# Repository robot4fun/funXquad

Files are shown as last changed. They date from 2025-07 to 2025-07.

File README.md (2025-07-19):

<p align="center">
  <picture>
    <source media="(prefers-color-scheme: dark)" srcset="funxedu-logo4-white.png">
    <source media="(prefers-color-scheme: light)" srcset="funxedu-logo4-black.png">
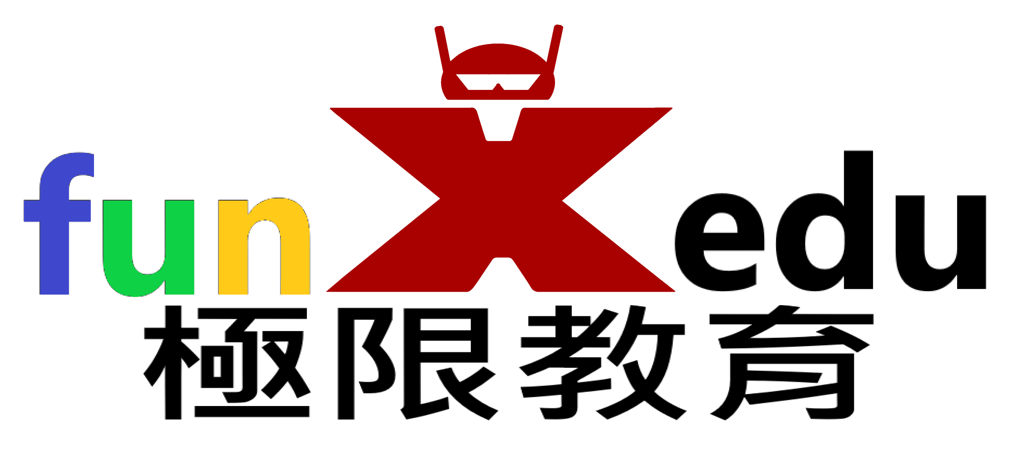
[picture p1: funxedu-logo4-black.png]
funXedu
    
  </picture>
  <br/>
</p>

funXquad 是一個低成本、DIY（自己動手做）的無人機項目，專為教育用途設計。

!! 此專案授權僅限個人或學校教學非商業用途。嚴禁任何商業使用、分發或用於商業目的之修改 !!

## 專案目錄結構

以下是 funXquad 專案的主要目錄及其功能：

* `frames/`: 無人機機架的3D列印檔案。

* `v1/`: 專案的第一個版本。
    * `firmware/`: 存放無人機的韌體檔案。
    * `hardware/`: 包含硬體設計檔案，例如電路圖或佈局檔案。

* `funXcon/`: 遙控器程式及相關文件。

* `README.md`: 專案的說明文件。

## DIY 材料清單

有室內和室外兩種類型，除電路板相同外，其餘零件不同。

* `電路板`:
    * `必要`:
        * `洞洞板`: 1個
        * `電池接頭`: 依電池規格 1個
        * `WiFi SOC`:
            * v1: `ESP12S模組` 1個
            * v2: 增加圖傳，努力中..
        * `IMU`: `MPU6050模組` 1個
        * `電晶體`: SI2302 或 NCE3420 4個
        * `二極體`: 1N4148 或 1N5819 4個
        * `電阻`: 1k歐姆以上 4個
        * `電量感測`； 10kΩ以上 1個 + 5倍阻值的電阻 1個
        * `電線`: 少許
    * `選用`:
        * `穩壓模組`:  如果選擇帶有 `3.3V 穩壓晶片` 的 `MPU6050模組` ，可以直接拉出 `3.3V電源` 供電給WiFi SOC。如果沒有，就需要 `1.8V-5V 轉 3.3V 穩壓模組` 1個
        * `室外高度計`: 3.3V BMP280模組 1個
        * `室內高度計`: VL53L0X模組 1個

* `機架`:
    * `室內機`: typeD 需牙籤 1支，切割成10mm長度共 4支
    * `室外機`: 3mmx3mmx500mm 碳纖維空心方管 1支，切割成50mm長度共 4支

* `動力系統`： 需4組
    * `室內機`: 820或8520空心杯馬達直驅 55mm 或 40mm 螺旋槳。螺旋槳孔徑需搭配馬達軸徑，通常是 1mm
    * `室外機`: 馬達採用720空心杯 + 減速齒輪組 + 135mm 螺旋槳。螺旋槳孔徑和形狀需搭配齒輪組軸徑    

* `電池`: 以下為實驗過的建議組合，注意電池和充電器接口需匹配
    * `室內機`: 3.8V 高壓 300mAh 75C 或 380mAh 60C 鋰電池 + 3.8V 充電器
    * `室外機`: 3.7V 600~1100mAh 20C + 3.7V充電器

## 所需工具
* `3D列印機`: 用於製作機架
* `燒錄器`: 用於燒錄韌體
* `焊接工具`: 用於製作電路板
* `熱熔膠槍`: 用於固定馬達，電路板和機架
* `橡皮筋`: 用於固定電池
* `安卓手機`: 用於遙控器安裝

## 製作機架
* 3D 打印零件，檔案在 [`frames`](/frames) 目錄內
* `室內機`:
    * `TypeB`: 共3個打印件
    * `TypeD`: 共3個打印件
    * `TypeE`: 1個打印件

* `室外機`: 共3個打印件
* 初學者建議使用 `PETG` 線材，機架會較有彈性，較耐撞摔

## 燒錄韌體
* `v1`: 
    * 下載韌體檔案 [ `firmware.bin` ](v1/firmware/firmware.bin)
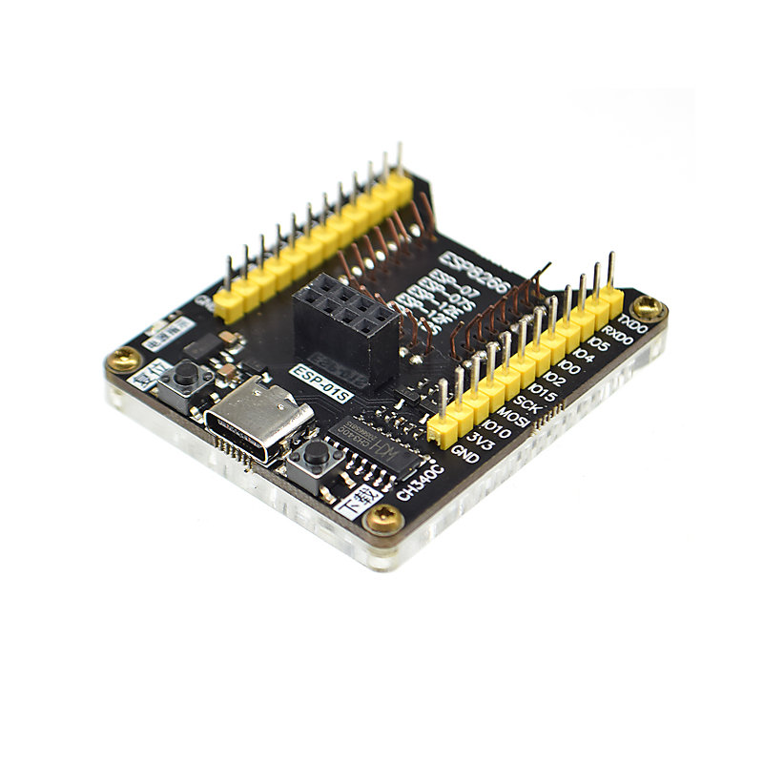
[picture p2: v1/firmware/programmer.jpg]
    * 將`ESP12S模組`正確放入 `燒錄器` 中  (如果使用 `USB to TTL` 或 `開發板` 當燒錄器，請確保接線和電壓正確)

    * 以 `USB 訊號線` (不是充電線) 連接 `電腦` 和 `燒錄器` 
    * 點選進入 [`燒錄工具網頁版`](https://espressif.github.io/esptool-js/)
    * 點選網頁 `Connect` 按鈕，選擇正確的`USB端口` 後點選 `連線`
    * `Flash Address` 設為 `0x0`
    * 點選 `選擇檔案` 按鈕後選擇之前下載的韌體檔 `firmware.bin`
    * 點選網頁 `Program` 按鈕後開始燒錄韌體
    * 燒錄完成後點選網頁 `Disconnect` 按鈕
    * 拔除 `USB` 線後取下 `ESP12S模組`

* `v2`: 增加圖傳，努力中..

## 製作電路板
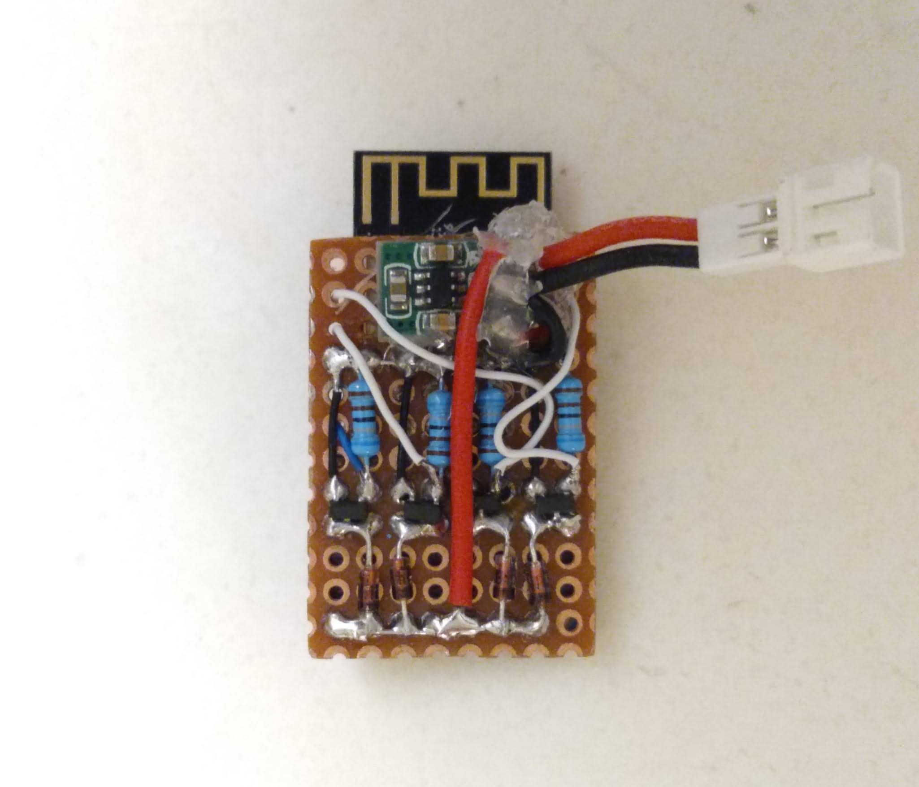
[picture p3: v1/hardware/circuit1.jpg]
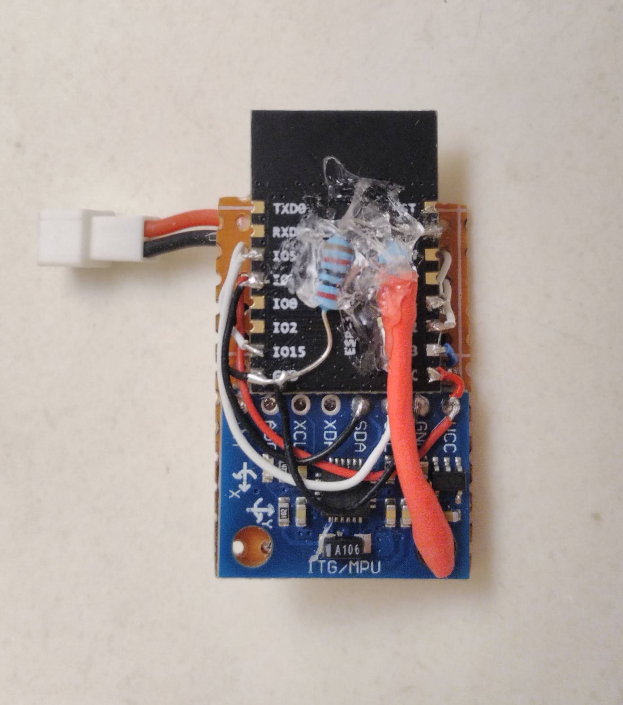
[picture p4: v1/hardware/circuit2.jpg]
* `v1`: 參照 [`原理圖`](v1/hardware/Schematic_funxdrone_v1.pdf) 和成品照自行加工 這張含 `穩壓模組` 

* `v2`: 增加圖傳，努力中..

## 組裝
* `室內機`: 
    
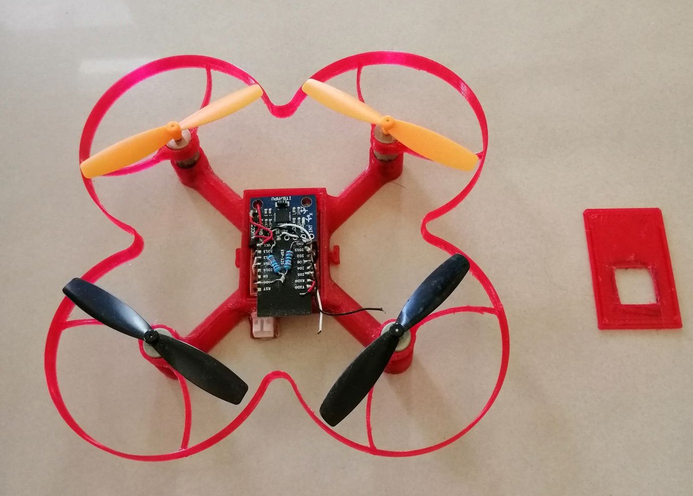
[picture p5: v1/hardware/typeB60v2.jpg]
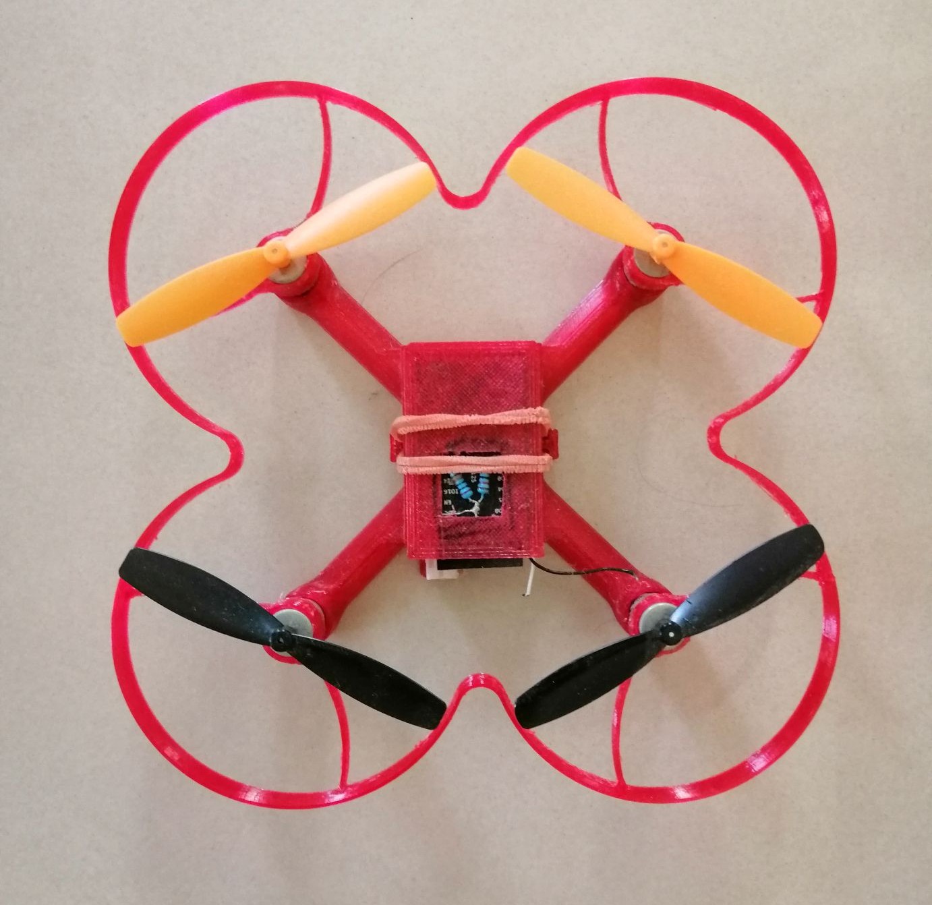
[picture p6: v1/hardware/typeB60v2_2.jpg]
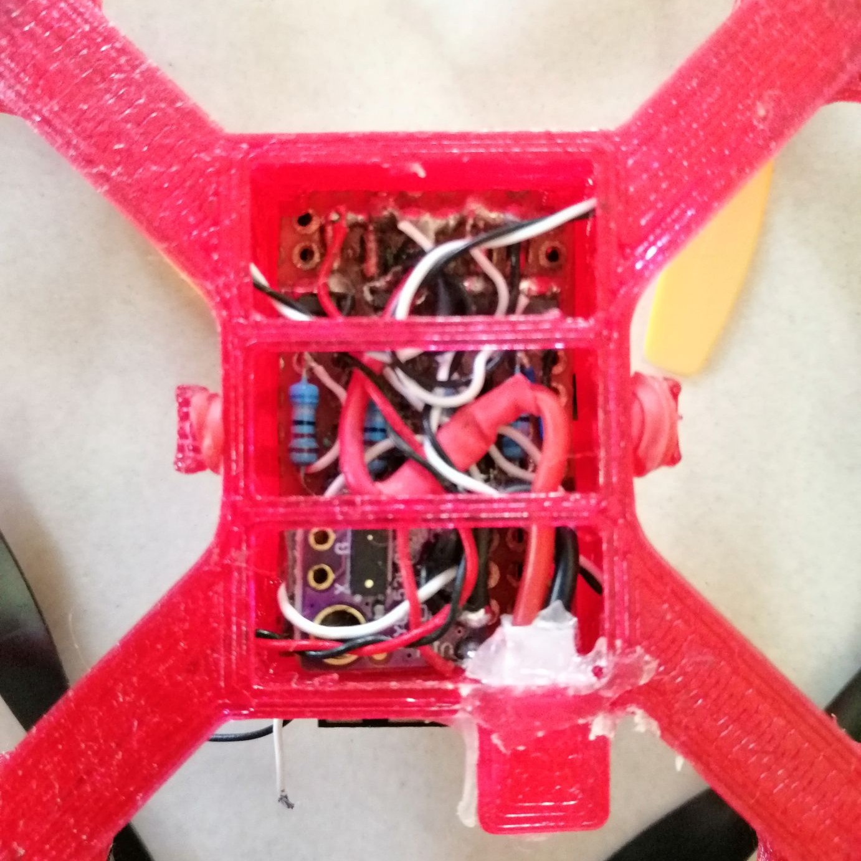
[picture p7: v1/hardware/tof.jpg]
    * `TypeB`: 適用 `55mm` 螺旋槳 這張電路板不含 `穩壓模組` ，由 `MPU6050模組` 自帶的 `3.3V 穩壓晶片` 穩壓 這張照片的螺旋槳是 `60mm`  裝了 `高度計`

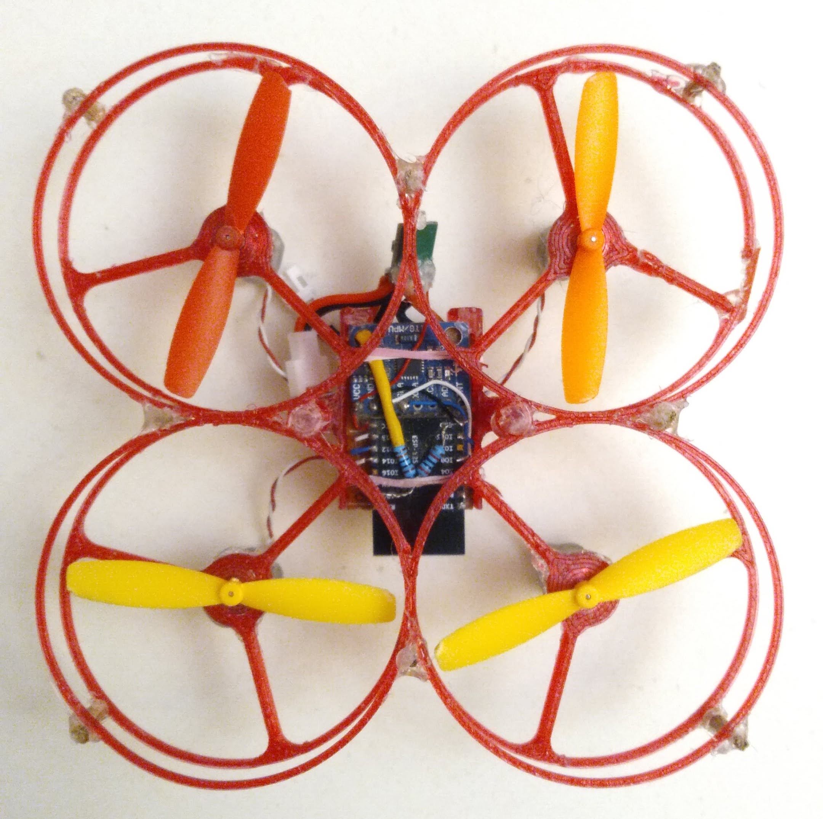
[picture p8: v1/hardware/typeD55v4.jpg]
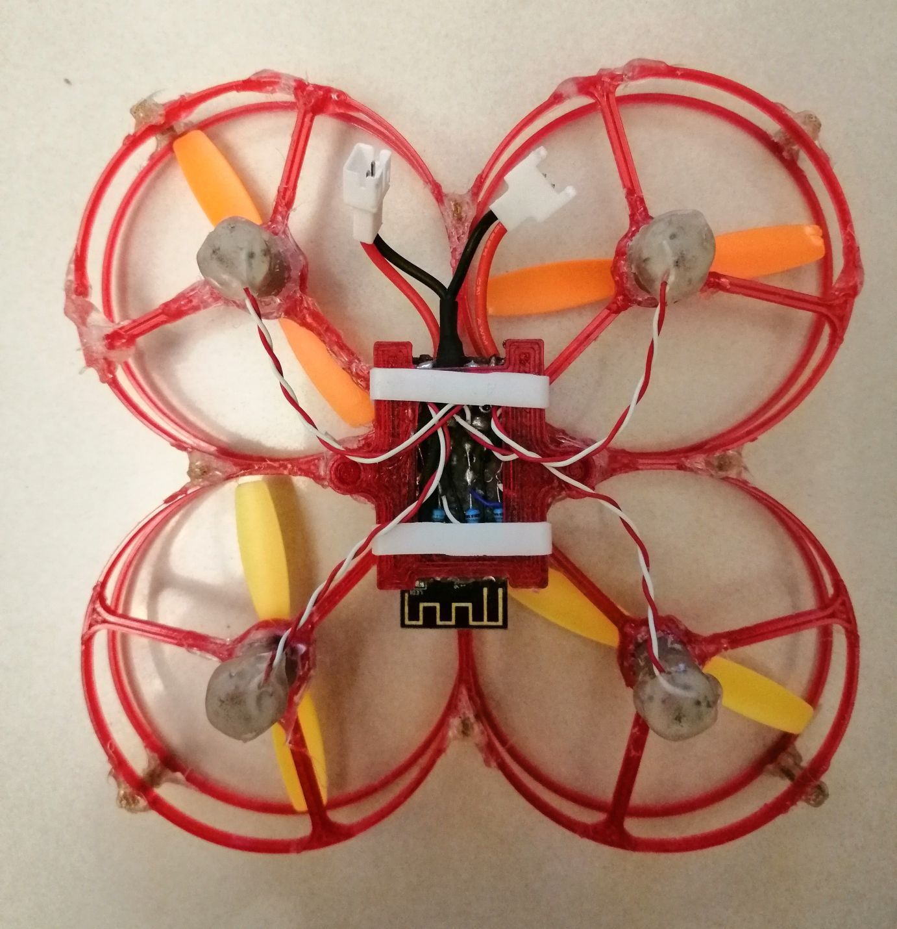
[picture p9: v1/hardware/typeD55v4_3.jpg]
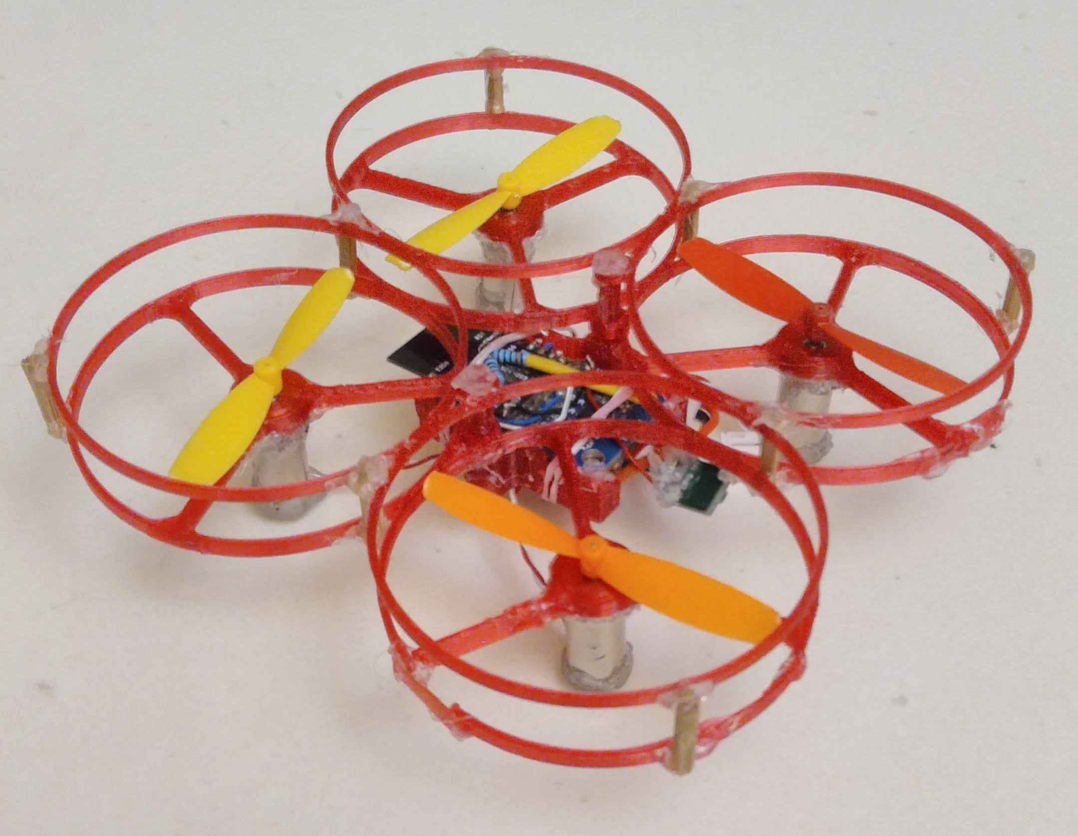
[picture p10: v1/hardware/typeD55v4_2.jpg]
    * `TypeD`: 適用 `55mm` 螺旋槳    
   
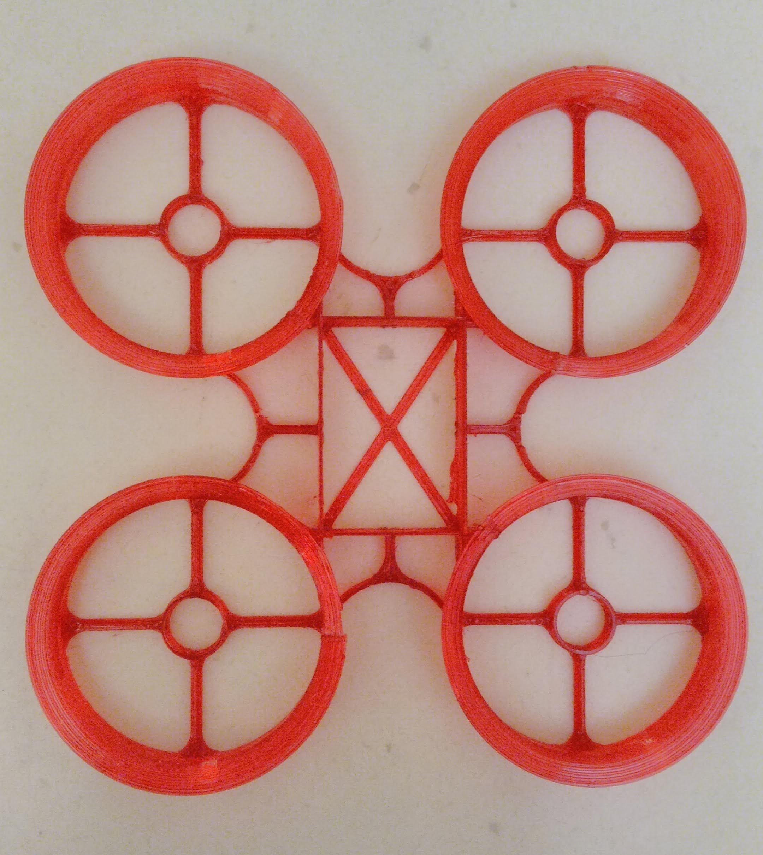
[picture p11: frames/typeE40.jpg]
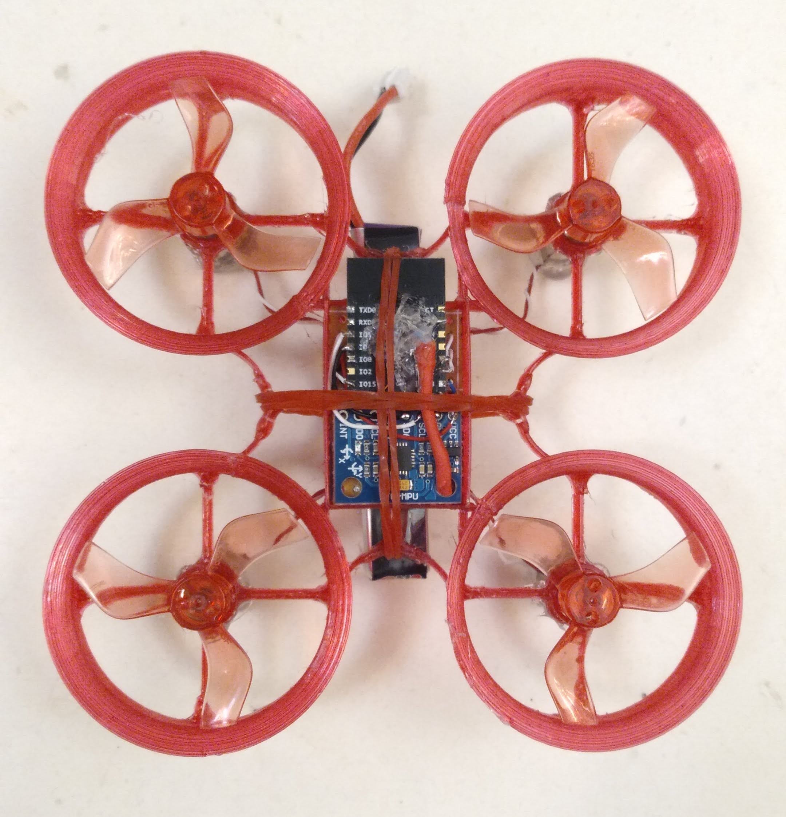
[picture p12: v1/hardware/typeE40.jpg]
    * `TypeE`: 適用 `40mm` 螺旋槳  

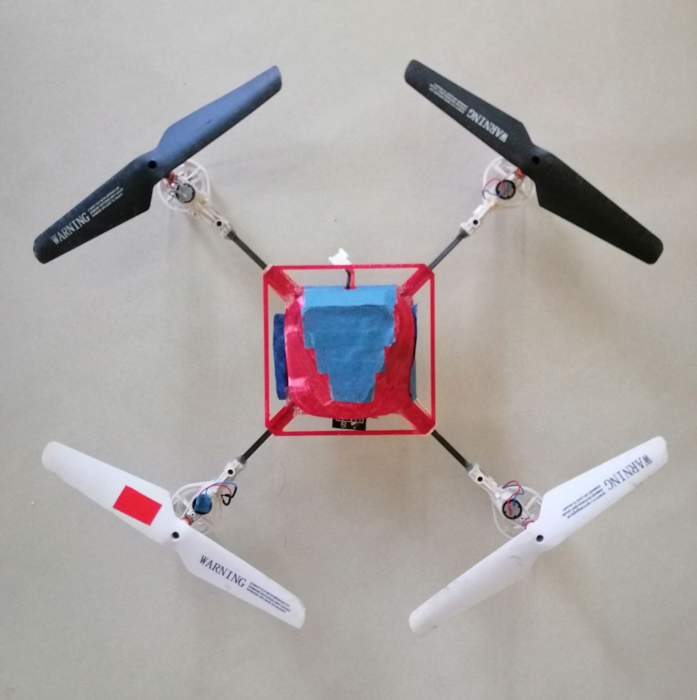
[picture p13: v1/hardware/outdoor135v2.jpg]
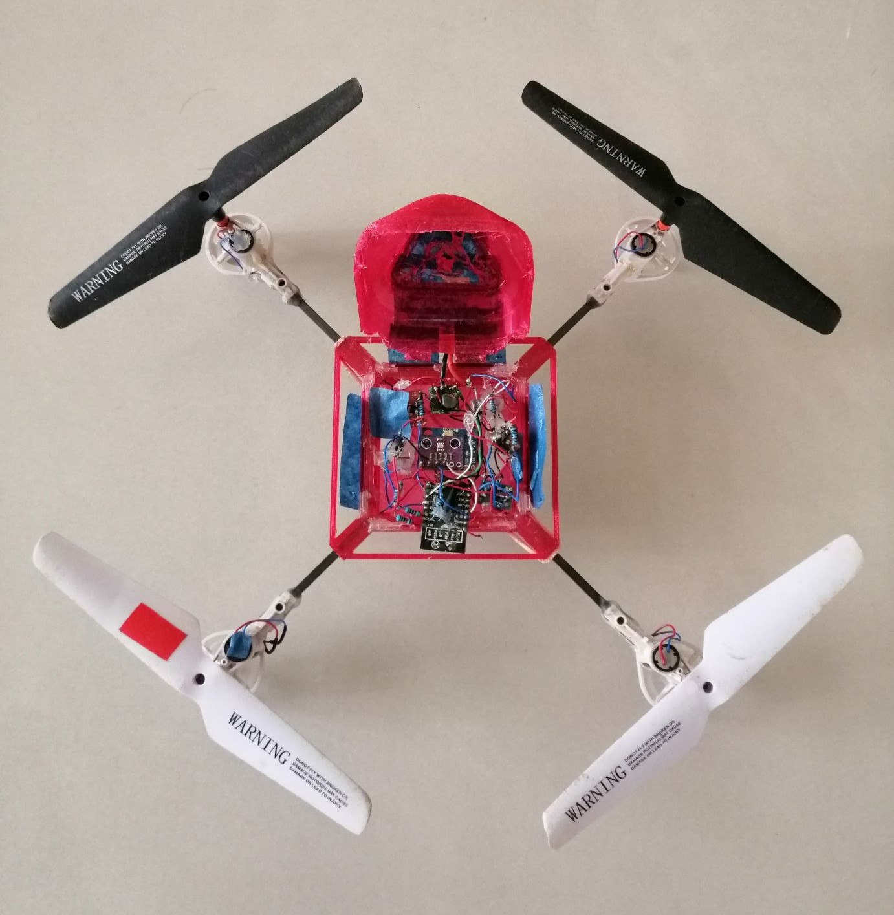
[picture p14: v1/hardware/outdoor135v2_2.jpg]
* `室外機`:   安裝了 `高度計` (線路凌亂，建議還是做好電路板再組裝)

## 遙控器
使用手機當遙控器，目前僅支持安卓10.0以下版本( 從 Android 10 開始，無法透過程式碼啟用或停用 WiFi )

* `安裝`: 先在手機內設定允許安裝不明程式，下載 [`funXcon.apk`](funXcon/funXcon.apk) 後安裝即可

* `使用說明`: 
    * 無人機插上電池 (天線是無人機的尾部)
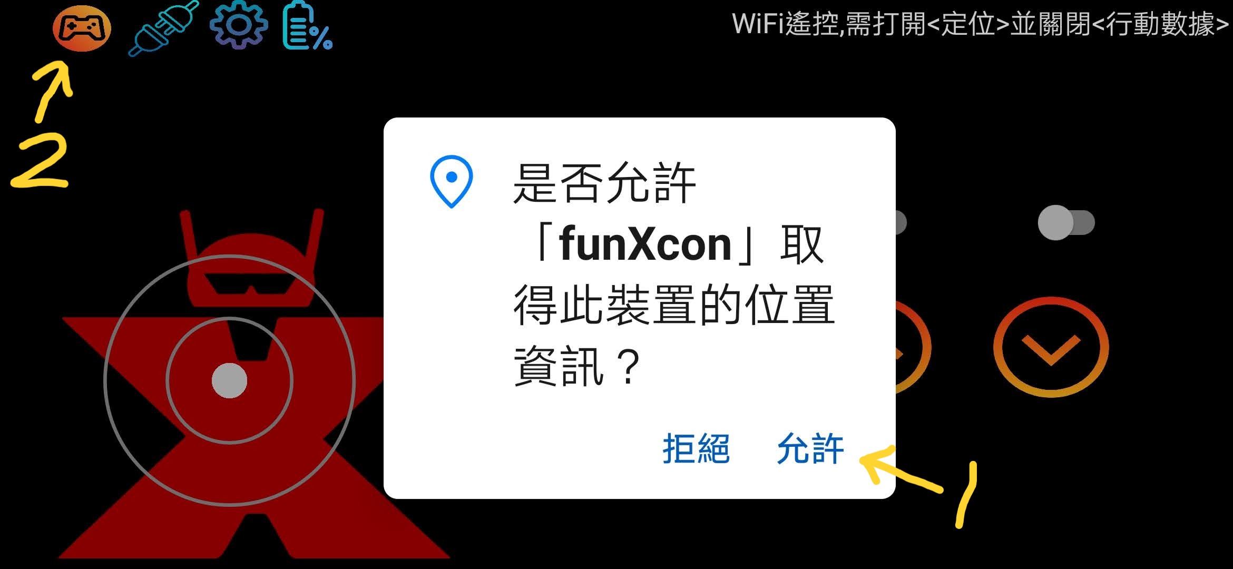
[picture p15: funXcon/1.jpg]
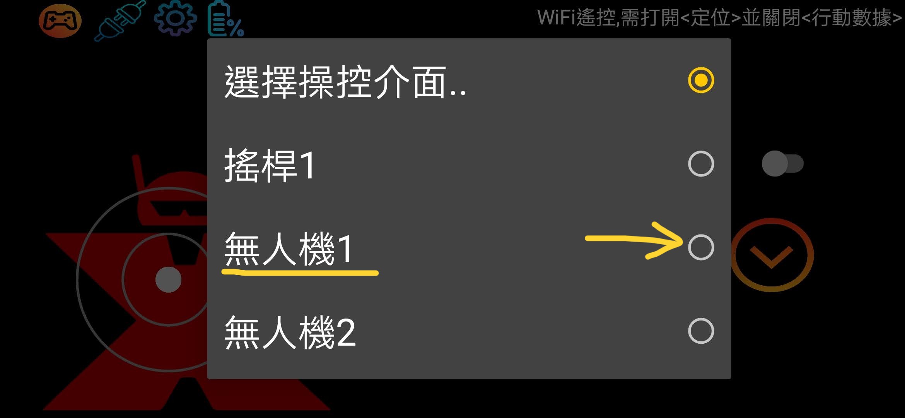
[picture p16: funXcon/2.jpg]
    * 因安卓系統問題，連接無人機的WiFi網路前須打開手機的 `定位服務` 並關閉 `行動數據`  
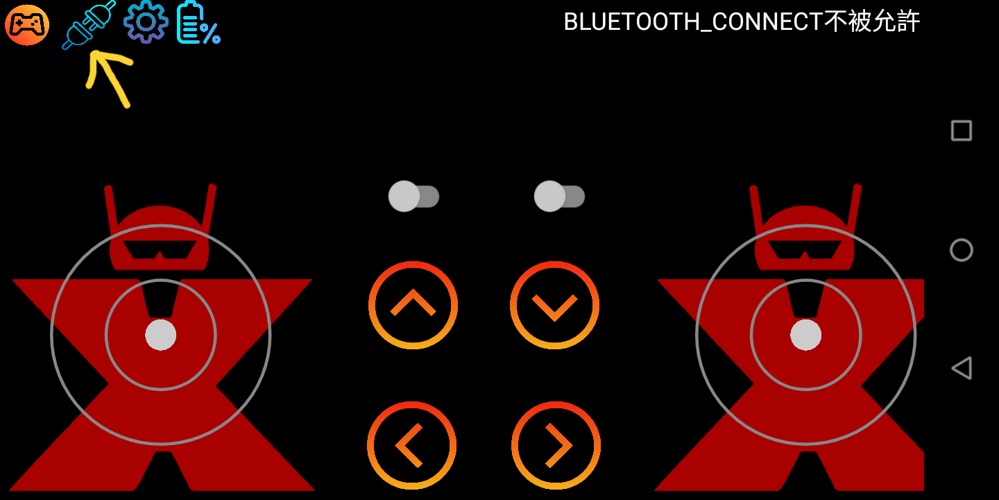
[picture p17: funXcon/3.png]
    * 按住 `插頭` 圖示不放以搜尋無人機，搜尋時圖示會變成 `雷達` 樣式 
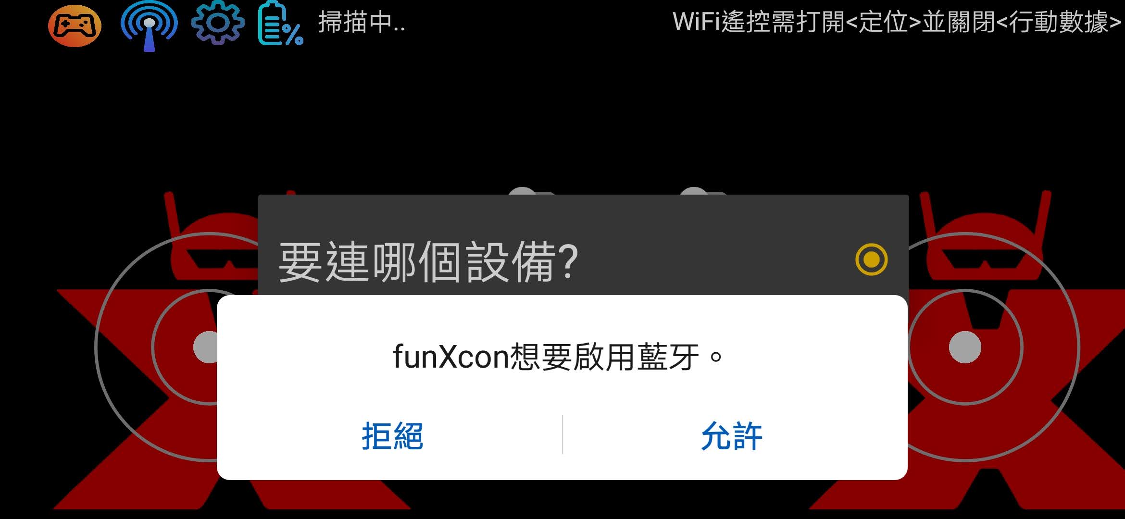
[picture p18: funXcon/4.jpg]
    * 出現藍牙警示時點選 `允許` 
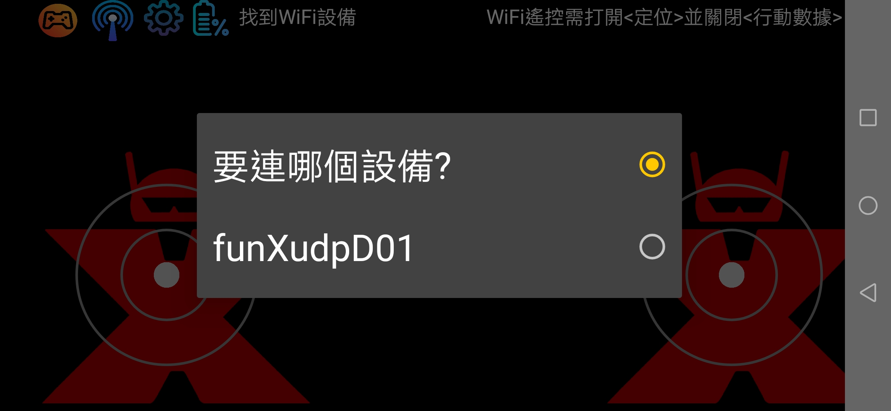
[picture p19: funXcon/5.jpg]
    * 搜尋到無人機後放開點選 `雷達` 圖示，然後選擇要連線的無人機編號 `funXudp00xx` (如果失敗，重按 `雷達` 圖示不放重新搜索即可) 
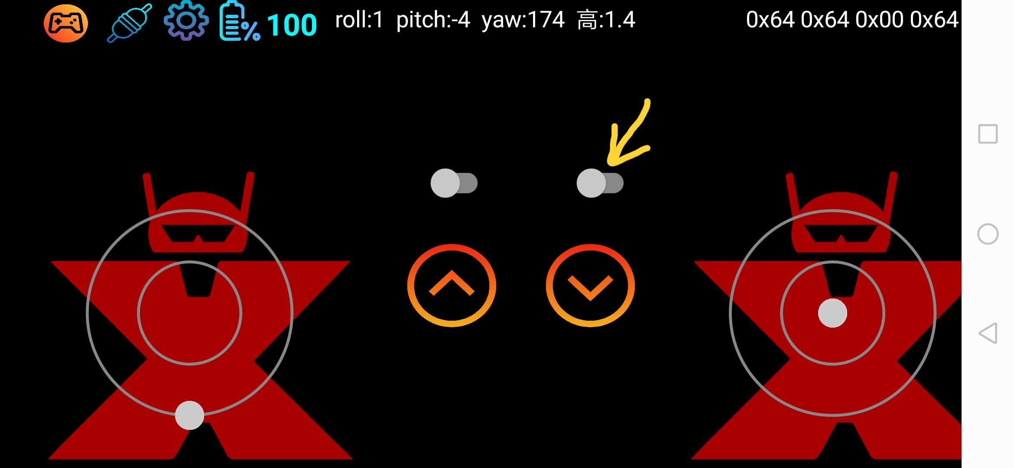
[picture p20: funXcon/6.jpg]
    * 連接成功後 `雷達` 圖示會變成 `插頭插入插座` 樣式，頂部會顯示無人機 `電池電量` 和 `姿態數據` ， `油門` 會設定到最小。確認安全後打開 `啟動開關` 啟動馬達 

    * 遙控器有四個控制桿，左邊是 `偏航`、`油門`，右邊是 `滾轉`、`俯仰` 
    * 電池電量不足時會響警報，關閉 `啟動開關` 會停止所有馬達
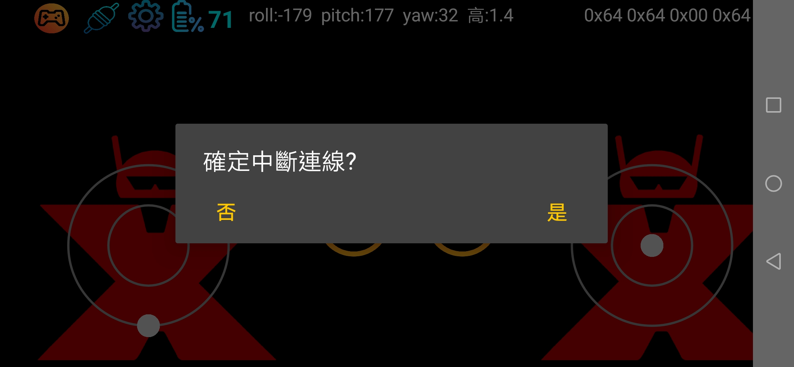
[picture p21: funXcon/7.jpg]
    * 不玩時請先關閉 `啟動開關` ，然後點選 `插頭` 圖示，等中斷連線後再拔除電池 

## 設定說明
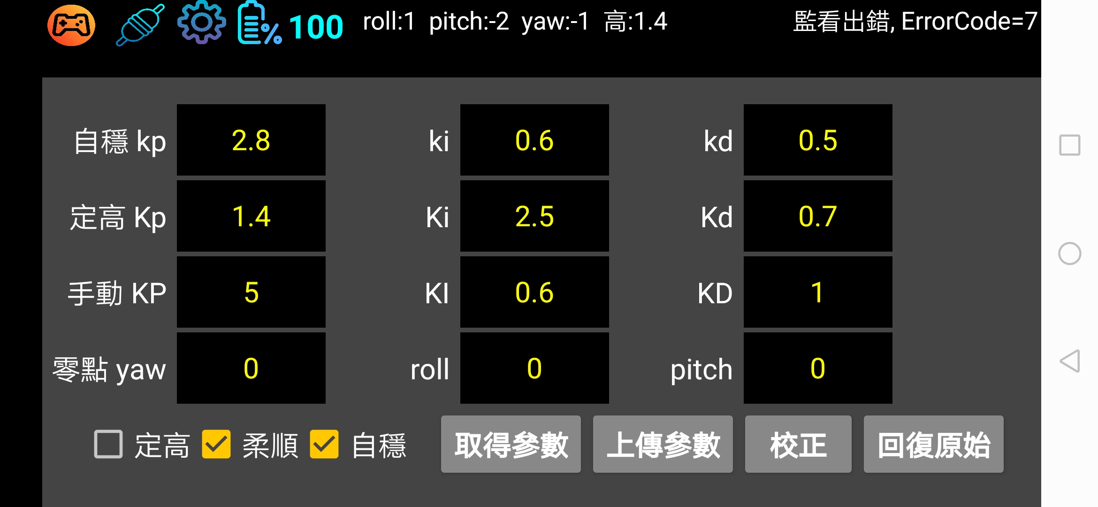
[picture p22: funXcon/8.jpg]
* 遙控器點選 `齒輪` 圖示會打開或關閉設定頁面 
* 除了 `校正` 選項外，其他選項都會影響飛行效果，請謹慎修改。
* `校正` 選項是用來校正無人機的姿態，請在無人機完全水平放置的情況下進行。
* 修改參數後須點選 `上傳參數` 按鈕才會生效。

## 注意事項
* 新手切勿修改 `設定值`。

* 打開 `啟動開關` 前 `油門` 要最小，以防意外。        

* 飛行中小心不要關閉 `啟動開關` ，否則..........悲劇囉!!

* 飛行超出遙控信號範圍時會自動緩慢降低高度，下降過程若進入信號範圍可繼續遙控飛行。如果一直超出信號範圍會下降直至落地。
    
* 如果安裝了`高度計`，可以打開 `定高開關` 定高飛行。但因為 `高度計` 的精度和算法問題，定高效果不會很好。新手不要輕易嘗試。

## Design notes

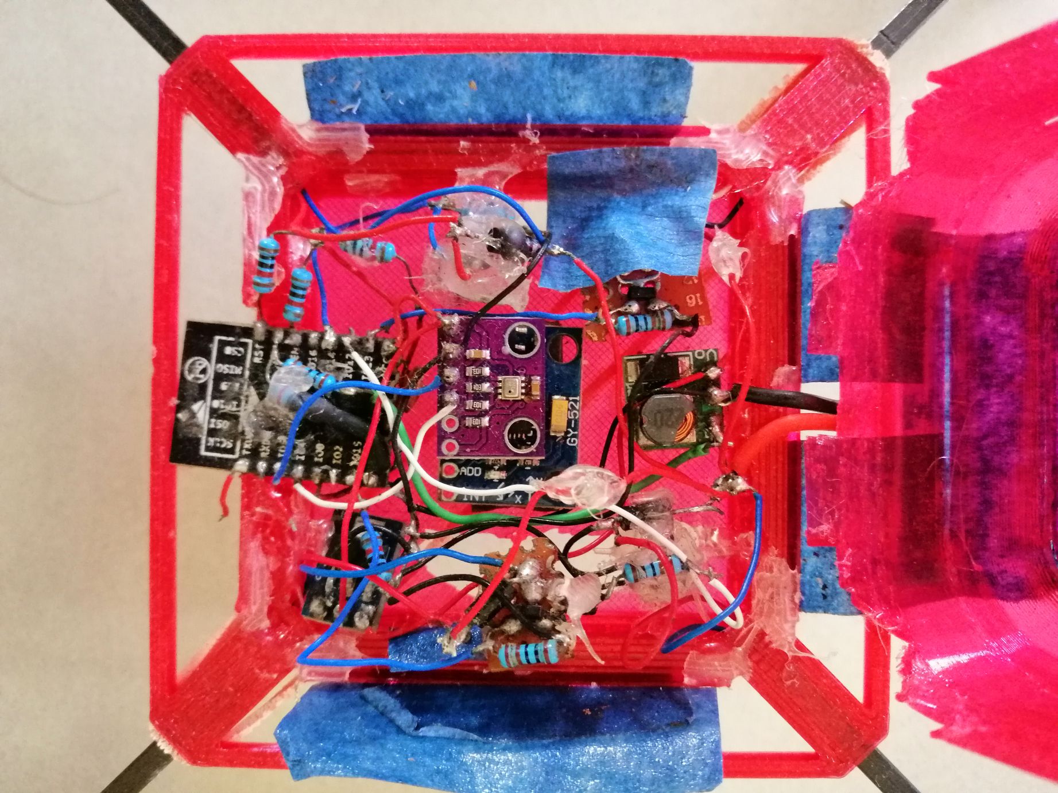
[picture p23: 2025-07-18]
v1/hardware/bmp280.jpg

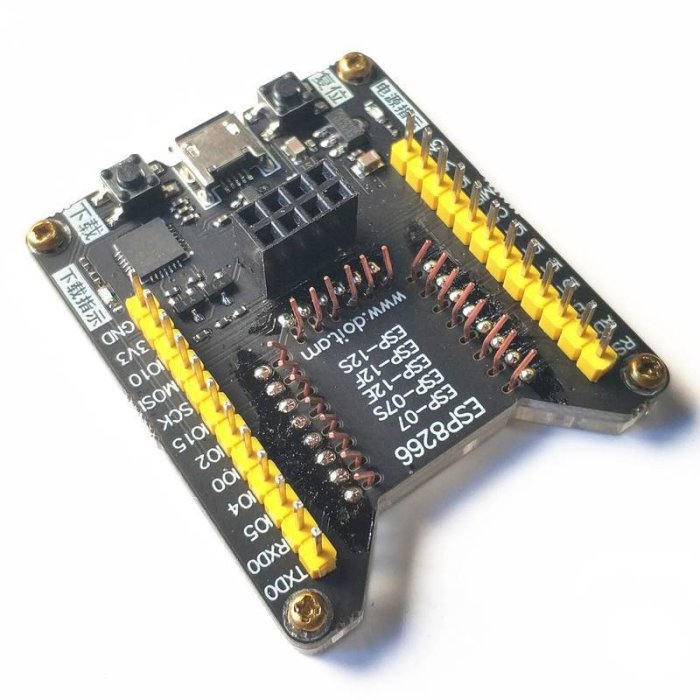
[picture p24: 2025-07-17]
v1/firmware/programmer2.jpg

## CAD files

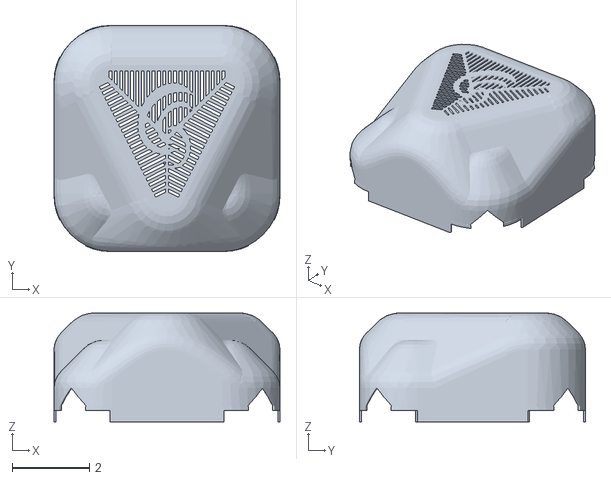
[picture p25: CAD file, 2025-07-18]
frames/outdoor135cover.stl
5.87 x 5.87 x 2.83

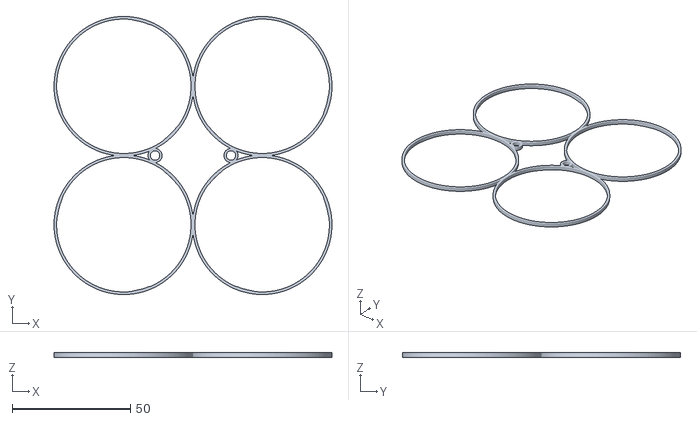
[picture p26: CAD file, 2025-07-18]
frames/typeD55v4d.stl
117.5 x 117.5 x 2.00

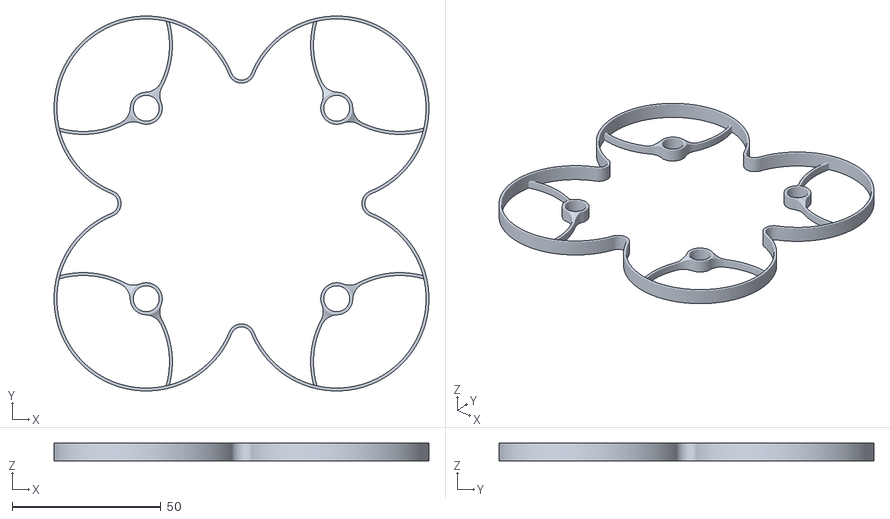
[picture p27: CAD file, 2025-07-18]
frames/typeBpropguard90mm.stl
126.0 x 126.0 x 6.00

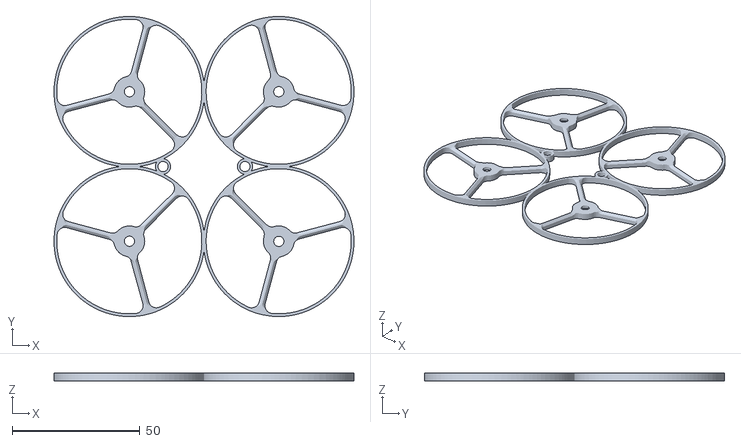
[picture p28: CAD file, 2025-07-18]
frames/typeD55v4.stl
117.5 x 117.5 x 2.99

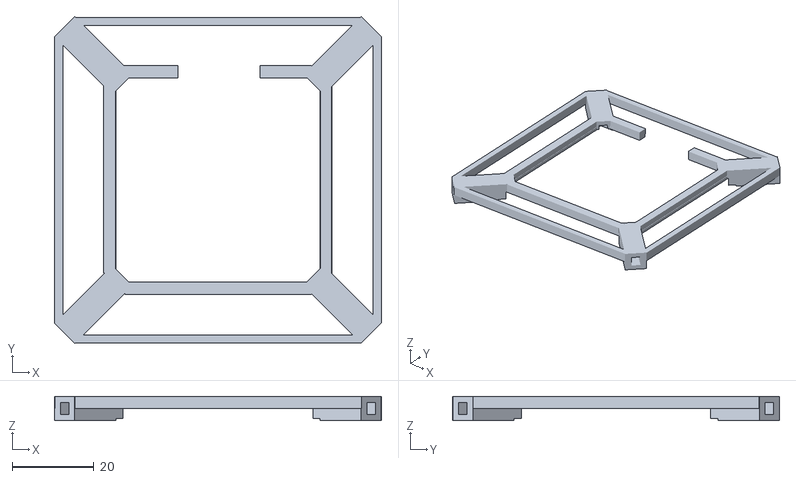
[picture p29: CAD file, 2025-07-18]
frames/outdoor135v2.stl
80.2 x 80.2 x 6.00

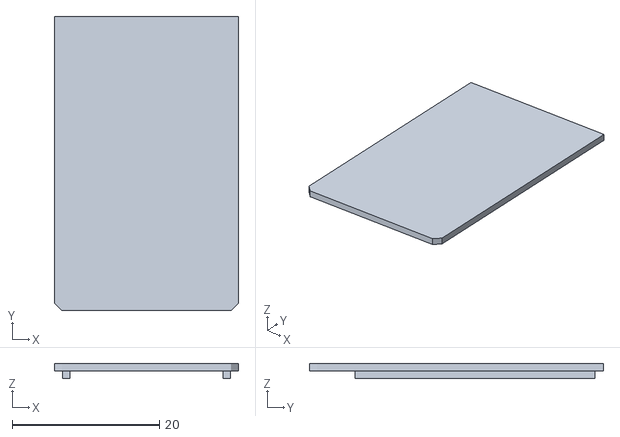
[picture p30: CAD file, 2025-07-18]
frames/typeBcover.stl
25.0 x 40.0 x 2.00

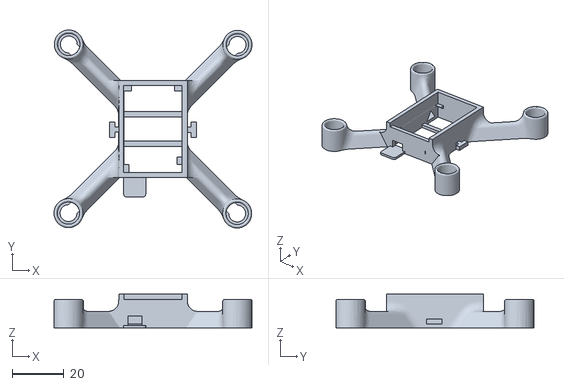
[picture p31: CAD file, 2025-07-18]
frames/typeB60v2.stl
76.3 x 76.3 x 13.0

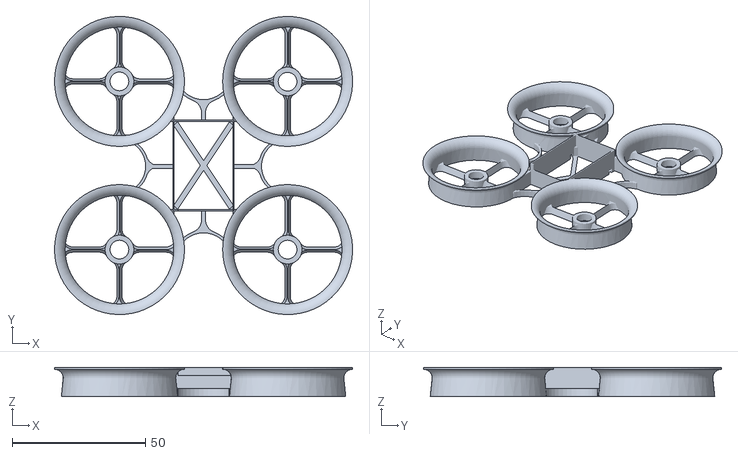
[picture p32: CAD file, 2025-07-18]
frames/typeE40.stl
111.7 x 111.7 x 11.0

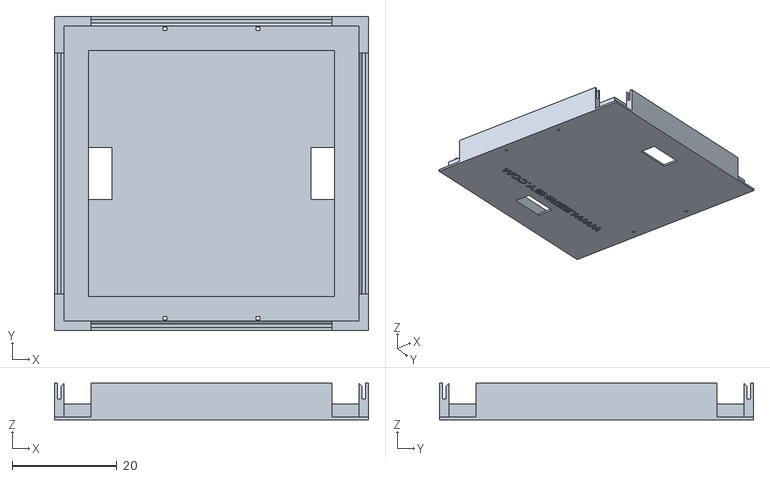
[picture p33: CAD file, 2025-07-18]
frames/outdoor135bottom.stl
60.0 x 60.0 x 7.00

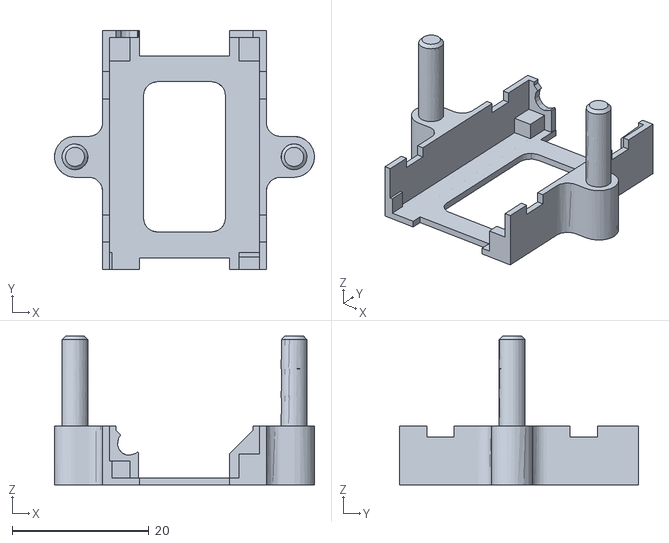
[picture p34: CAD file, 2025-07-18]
frames/typeD55v4fcTray1.stl
38.1 x 35.0 x 21.8

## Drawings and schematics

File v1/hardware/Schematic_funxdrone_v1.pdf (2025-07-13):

## GND

POWER | MOTORs

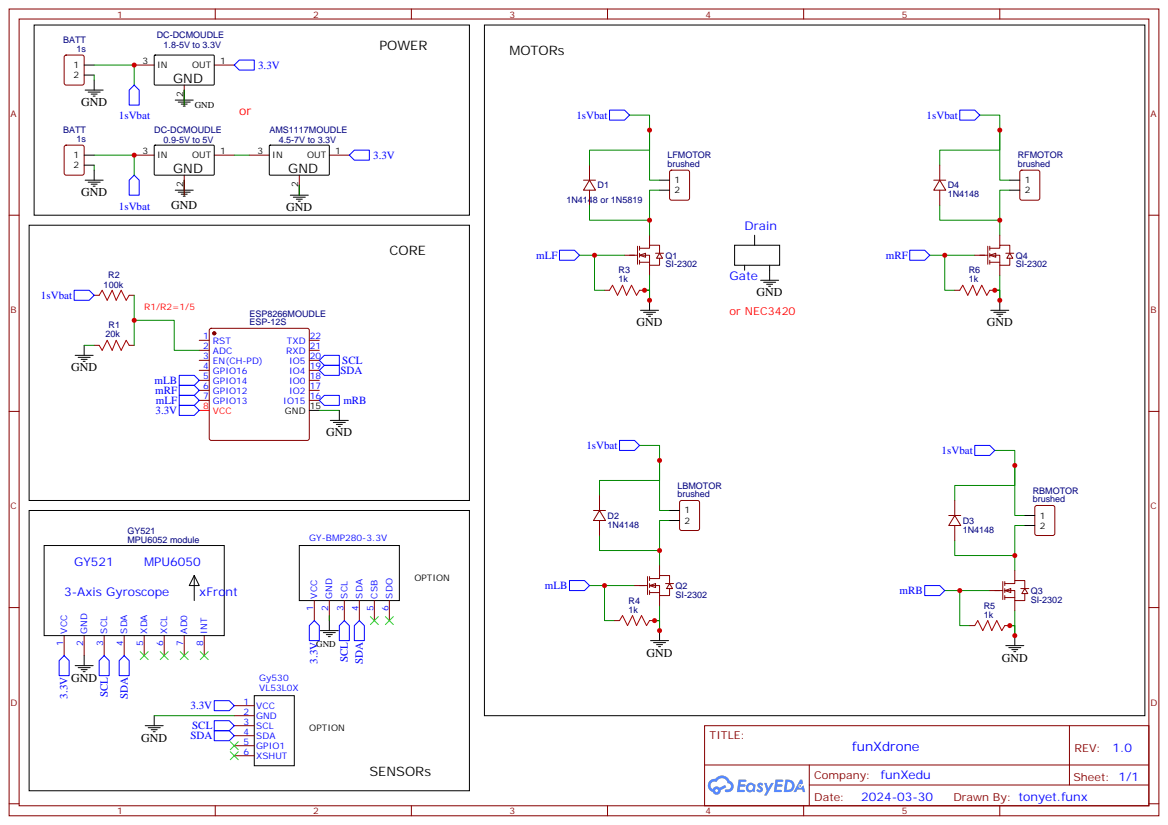
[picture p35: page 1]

Drawn By: tonyet.funx

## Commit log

2025-07-13 readme編寫中
2025-07-17 docs(README): 更新 funXquad 項目說明書
    - 添加了目錄結構的詳細說明
    - 補充了所需工具的列表
    - 新增了機架製作、韌體燒錄、電路板製作和組裝的步驟说明
    - 調整了部分文字格式，使其更加清晰易讀
2025-07-18 docs(README): 更新專案说明和使用指南
    - 添加项目logo和更正授权说明
    - 补充遥控器使用说明和注意事项
    - 更新机架和电路板制作指南
    - 移除部分冗余图片
    [outdoor135bottom.stl, outdoor135cover.stl, outdoor135v2.stl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]
2025-07-18 docs(README): 更新無人機組裝和燒錄教程
    - 補充室外機螺旋槳規格說明
    - 更新燒錄工具使用步驟
    - 移除不必要的硬件圖片
    - 重新命名螺旋槳圖片
    - 更新遙控器安裝和使用說明
    - 添加注意事項提示
    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
2025-07-18 README.md中強調USB訊號線
2025-07-19 docs(README): 更新無人機項目说明
    - 調整初學者建議使用的線材描述，更準確地描述 PETG 線材的特性
    - 更新韌體下載方式，提供直接下載链接
    - 添加 TypeD 機型的额外照片
    - 更新遙控器安裝说明，提供直接下載链接
    - 增加設定說明部分，提醒新手謹慎修改設定值
    - 添加新手注意事項，確保安全使用
    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
2025-07-19 docs(README): 更新室外機動力系統说明
    - 在室外機部分添加了動力系統的詳細說明
    - 移除了不必要的圖片鏈接，使內容更加清晰
    - 調整了部分文字格式，提高了可讀性
2025-07-19 docs: 更新 README 中的 logo 图片- 根据不同的颜色主题动态显示对应的 logo
2025-07-19 刪除logo下一列空白行
